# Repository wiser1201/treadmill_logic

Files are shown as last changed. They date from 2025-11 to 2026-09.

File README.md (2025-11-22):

# Description

This project replaces the entire logic/control section of a broken treadmill with a custom-designed **STM32** microcontroller-based control system. The power electronic part of the original board stayed intact, but the control MCU and interface electronics were redesigned to restore full functionality and improve usability. Firmware is written in **C** using **HAL** library and register access when needed.

IMG_treadmill

IMG_UI

# Hardware

### Components

- **Power PCB:** Reused robust power part of the original board;
- **Logic PCB:** Designed board that contains low-voltage supply + control logic;
- **Interface PCB:** Contains three buttons, and LCD 16x2;
- **MCU:** STM32 F103C6T6;

### Architecture

System uses phase angle control topology. The original power board contains an optocoupler that triggers a triac driving the 220 VAC power rail. After each zero-cross event, the triac naturally turns off; the moment at which it is fired determines what portion of each AC half-wave reaches the motor.

The logic PCB generates a zero-cross pulse using a transformer (13 VAC), rectifier, and an optocoupler. When the AC waveform rises above the LED threshold (~1.2 V), the optocoupler produces a clean pulse that marks each zero-crossing. STM32 receives this pulse, TIM1 in one pulse slave mode starts counting a delay automatically, and then, in the end of the delay, fires a short trigger pulse to the power-stage optocoupler, which in turn fires the main triac.

Motor speed is closed-loop controlled. The PID controller adjusts delay of TIM1 based on the current speed, calculated via RPM and a belt length. If current speed lower than target, PID decreases TIM1 delay, that gives more power to the triac. And vice versa.

# Software

### Architecture

Almost all software is divided into two layers: driver and application. 

- **Driver layer.** Low level code related to peripheral configuration, peripheral initialization.

- **Application layer.** Code, that's not related or not only related to peripherals. Software that built on top of the drivers, and corresponds to one specific use.

Some modules (such as simple Buttons or Buzzer) are too small to justify a strict driver/application separation. In these cases, the functionality is implemented in a single combined module to keep the code clean and avoid unnecessary fragmentation.

### Main loop

IMG_loop

The main loop coordinates the system's high-level tasks: motion control, fault monitoring, button handling**, **buzzer control, and LCD updates:

- **motion.** Executes the PID-based speed control described earlier, updating the phase-angle delay according to the current RPM feedback.
- **fault_check.** Monitors critical runtime conditions. It ensures that tim3, hall sensor and motion control work correctly.
- **buttons_handler.** Polls the user interface buttons (Start/Stop, Speed+, Speed–), debounces input, passes information to the system module.
- **buzzer.** Non-blocking audible feedback system.
- **LCD.** Periodically updates the 16×2 LCD with four metrics: Calories (C), Speed (S), Time (T), and Distance (D). The update routine is optimized to refresh only changed fields.

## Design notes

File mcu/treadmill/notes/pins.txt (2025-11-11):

PA8 - ZERO_CROSS;
PA9 - Trigger;
PB6-8 - Buttons;
PB5 - Buzzer;
PA7-1 - LCD;
PB4 - Hall;

pcb:
4 gnd, 4 +5V: (lcd, mcu, hall, +1 extra);
2 signals: buzzer, ZERO_CROSS

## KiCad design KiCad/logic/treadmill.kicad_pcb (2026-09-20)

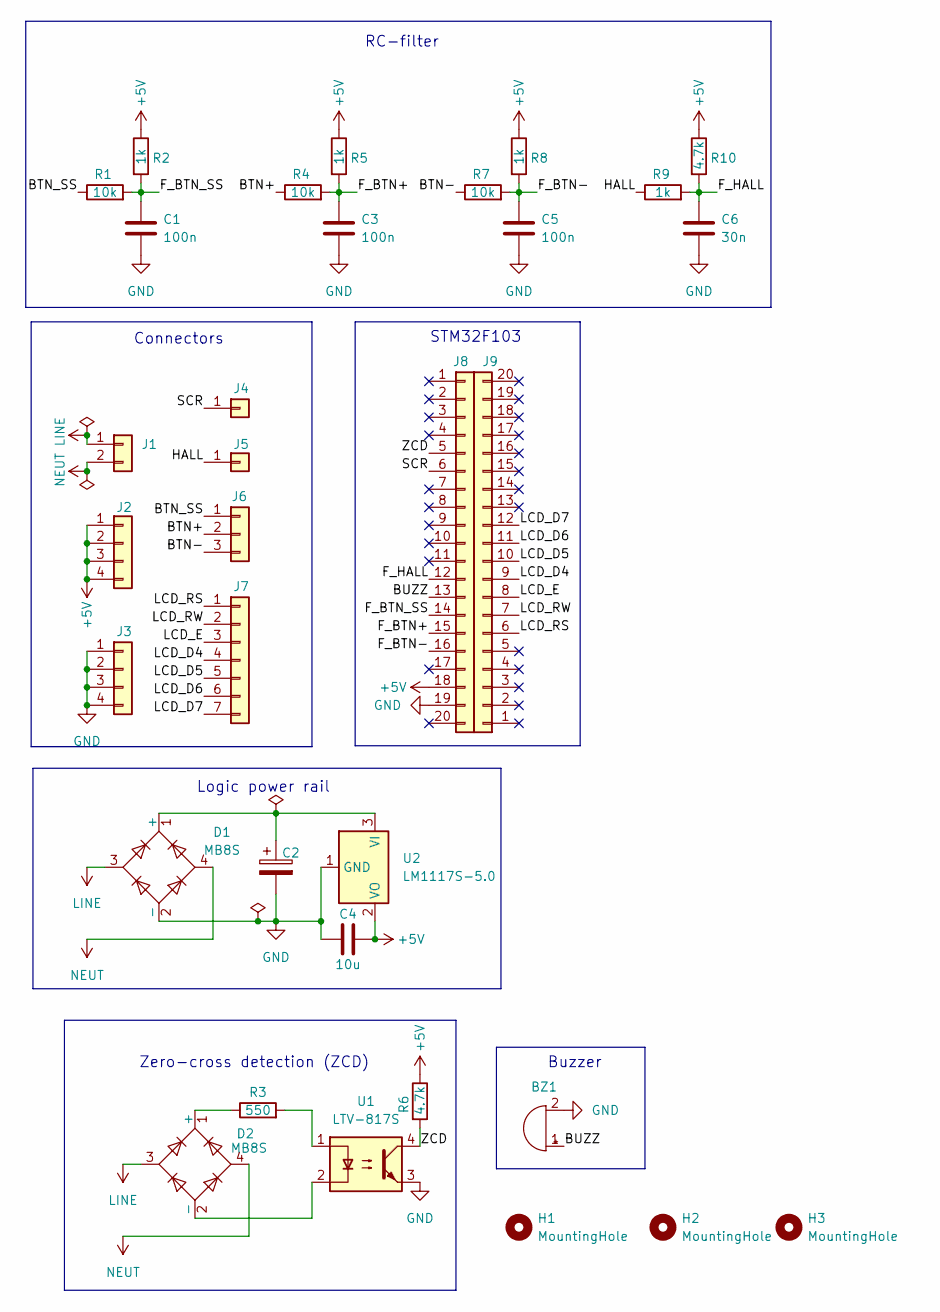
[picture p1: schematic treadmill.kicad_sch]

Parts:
BZ1: Buzzer; Buzzer_12x9.5RM7.6
C1, C3, C5: 100n; C_0805_2012Metric
C2: C_Polarized; CP_Radial_D13.0mm_P7.50mm
C4: 10u; C_0805_2012Metric
C6: 30n; C_0805_2012Metric
D1, D2: MB8S; OnSemi_751EP_SOIC-4_3.9x4.725mm_P2.54mm
H1, H2, H3: MountingHole; MountingHole_3.2mm_M3
J1: AC; TerminalBlock_Phoenix_MKDS-1,5-2_1x02_P5.00mm_Horizontal
J2: +5V; PinHeader_1x04_P2.54mm_Vertical
J3: GND; PinHeader_1x04_P2.54mm_Vertical
J4: SCR_01x01; PinHeader_1x01_P2.54mm_Vertical
J5: HALL_01x01; PinHeader_1x01_P2.54mm_Vertical
J6: BTN_01x03; PinSocket_1x03_P2.54mm_Vertical
J7: LCD_01x07; PinSocket_1x07_P2.54mm_Vertical
J8: MCU-1; PinSocket_1x20_P2.54mm_Vertical
J9: MCU-2; PinSocket_1x20_P2.54mm_Vertical
R1, R4, R7: 10k; R_0805_2012Metric
R2, R5, R8, R9: 1k; R_0805_2012Metric
R3: 550; R_2010_5025Metric
R6, R10: 4.7k; R_0805_2012Metric
U1: LTV-817S; SMDIP-4_W9.53mm
U2: LM1117S-5.0; SOT-223-3_TabPin2

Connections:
+5V: C4.2, J2.1, J2.2, J2.3, J2.4, J8.18, R2.1, R5.1, R6.1, R8.1, R10.1, U2.2 (VO)
/BTN+: J6.2, R4.1
/BTN-: J6.3, R7.1
/BTN_SS: J6.1, R1.1
/BUZZ: BZ1.1 (+), J8.13
/F_BTN+: C3.1, J8.15, R4.2, R5.2
/F_BTN-: C5.1, J8.16, R7.2, R8.2
/F_BTN_SS: C1.1, J8.14, R1.2, R2.2
/F_HALL: C6.1, J8.12, R9.2, R10.2
/HALL: J5.1, R9.1
/LCD_D4: J7.4, J9.9
/LCD_D5: J7.5, J9.10
/LCD_D6: J7.6, J9.11
/LCD_D7: J7.7, J9.12
/LCD_E: J7.3, J9.8
/LCD_RS: J7.1, J9.6
/LCD_RW: J7.2, J9.7
/SCR: J4.1, J8.6
/ZCD: J8.5, R6.2, U1.4
GND: BZ1.2 (-), C1.2, C2.2, C3.2, C4.1, C5.2, C6.2, D1.2 (-), J3.1, J3.2, J3.3, J3.4, J8.19, U1.3, U2.1 (GND)
LINE: D1.3, D2.3, J1.1
NEUT: D1.4, D2.4, J1.2
unnamed: C2.1, D1.1 (+), U2.3 (VI)
unnamed: D2.1 (+), R3.1
unnamed: D2.2 (-), U1.2
unnamed: R3.2, U1.1

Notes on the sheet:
Buzzer
Zero-cross detection (ZCD)
Logic power rail
Connectors
RC-filter
STM32F103

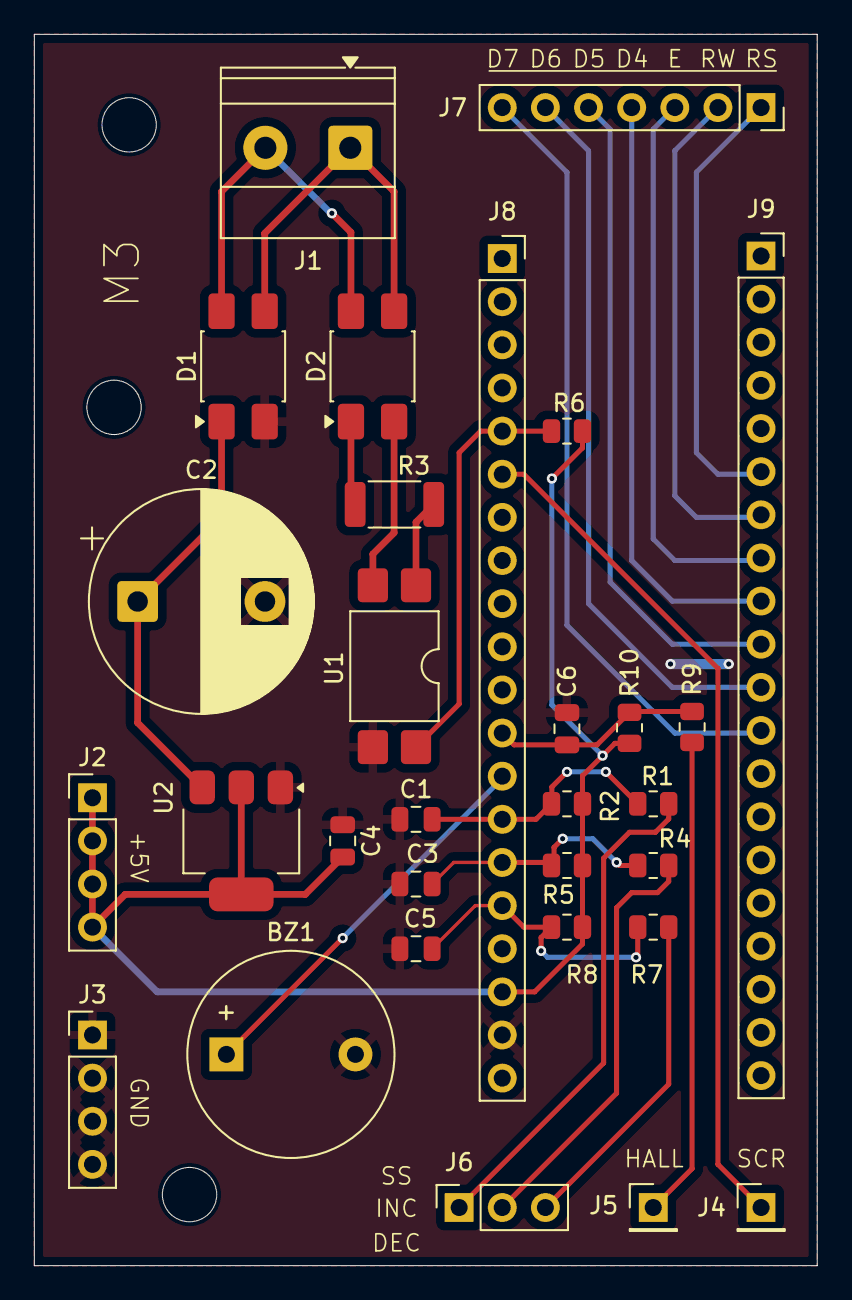
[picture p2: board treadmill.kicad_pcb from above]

Board: 2 copper layers, 46.1 x 72.5 mm, 33 parts (0 on the bottom side), 26 nets.

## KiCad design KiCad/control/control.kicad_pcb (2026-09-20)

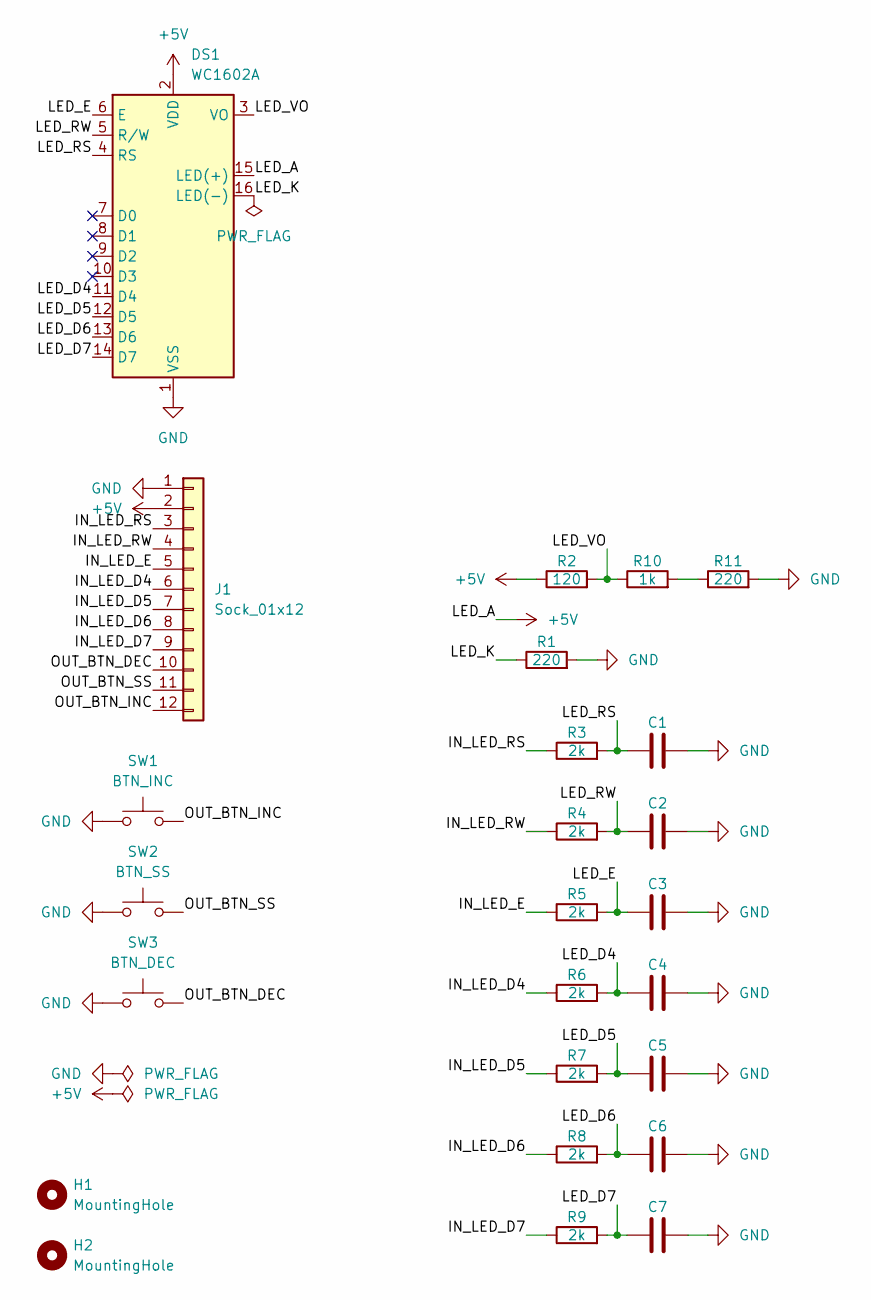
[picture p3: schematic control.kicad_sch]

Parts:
C1, C2, C3, C4, C5, C6, C7: 1n; C_0805_2012Metric
DS1: WC1602A
H1, H2: MountingHole; MountingHole_2.7mm
J1: Sock_01x12; PinSocket_1x12_P2.54mm_Vertical
R1, R11: 220; R_1210_3225Metric
R2: 120; R_1210_3225Metric
R3, R4, R5, R6, R7, R8, R9: 2k; R_0805_2012Metric
R10: 1k; R_1210_3225Metric
SW1: BTN_INC; SW_PUSH-12mm
SW2: BTN_SS; SW_PUSH-12mm
SW3: BTN_DEC; SW_PUSH-12mm

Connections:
+5V: DS1.2 (VDD), DS1.15 (LED(+)), J1.2, R2.1
/IN_LED_D4: J1.6, R6.1
/IN_LED_D5: J1.7, R7.1
/IN_LED_D6: J1.8, R8.1
/IN_LED_D7: J1.9, R9.1
/IN_LED_E: J1.5, R5.1
/IN_LED_RS: J1.3, R3.1
/IN_LED_RW: J1.4, R4.1
/LED_D4: C4.2, DS1.11 (D4), R6.2
/LED_D5: C5.2, DS1.12 (D5), R7.2
/LED_D6: C6.2, DS1.13 (D6), R8.2
/LED_D7: C7.2, DS1.14 (D7), R9.2
/LED_E: C3.2, DS1.6 (E), R5.2
/LED_K: DS1.16 (LED(-)), R1.1
/LED_RS: C1.2, DS1.4 (RS), R3.2
/LED_RW: C2.2, DS1.5 (R/W), R4.2
/LED_VO: DS1.3 (VO), R2.2, R10.1
/OUT_BTN_DEC: J1.10, SW3.2
/OUT_BTN_INC: J1.12, SW1.2
/OUT_BTN_SS: J1.11, SW2.2
GND: C1.1, C2.1, C3.1, C4.1, C5.1, C6.1, C7.1, DS1.1 (VSS), J1.1, R1.2, R11.2, SW1.1, SW2.1, SW3.1
unnamed: R10.2, R11.1

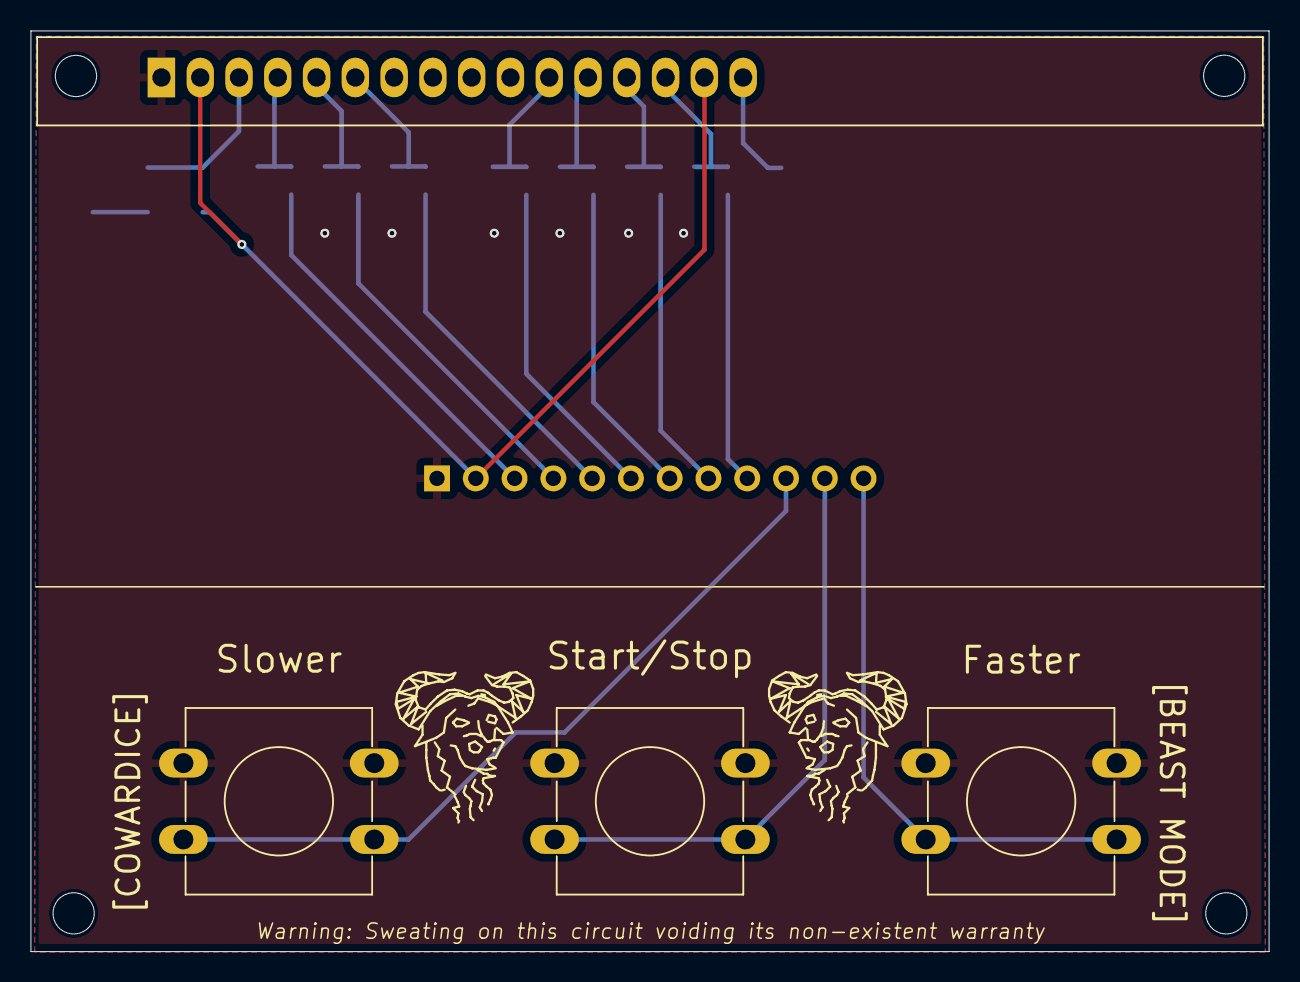
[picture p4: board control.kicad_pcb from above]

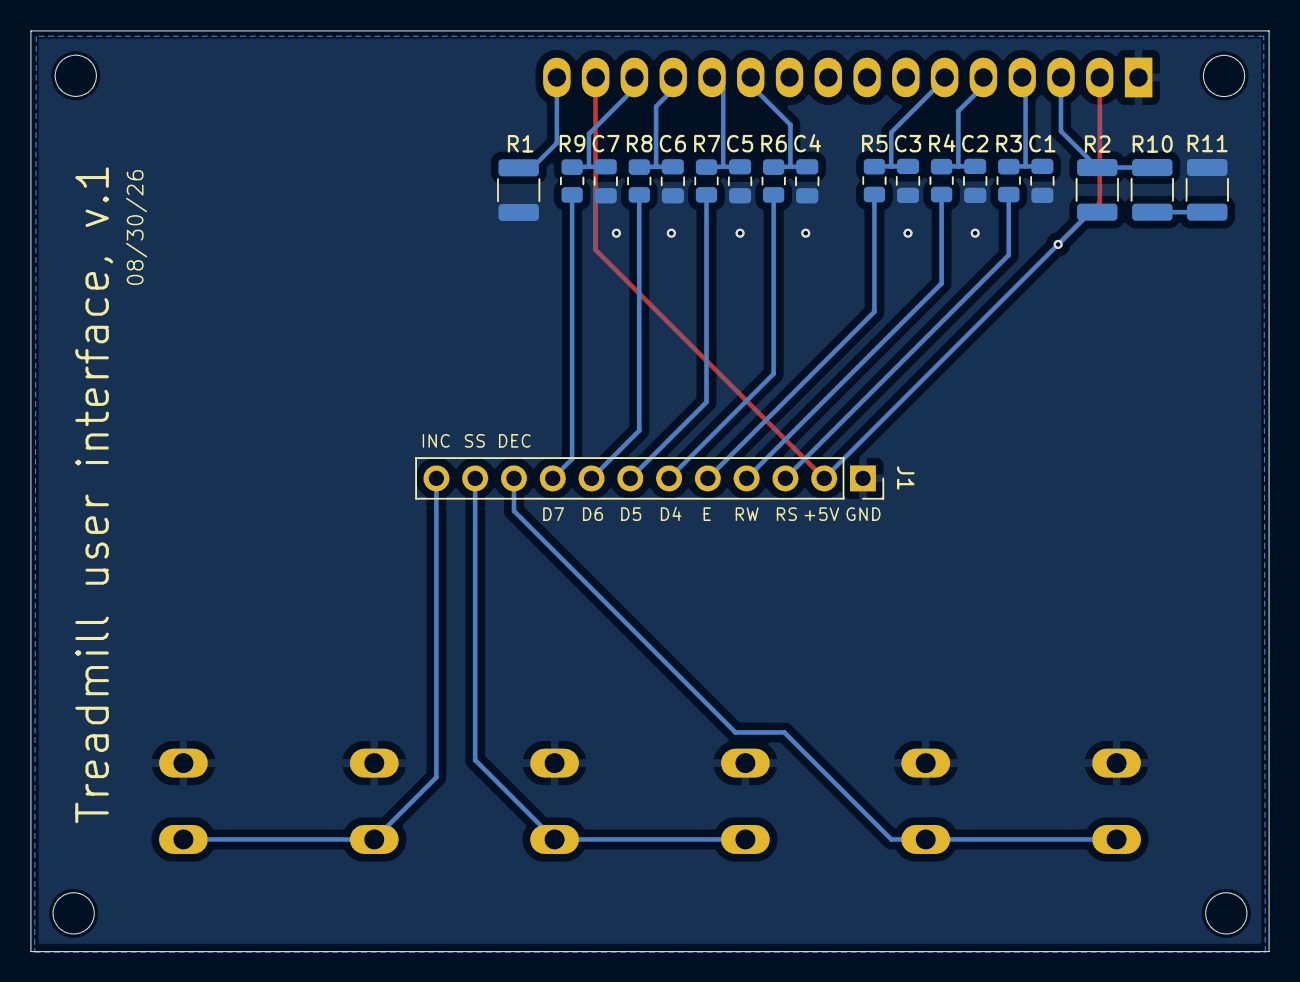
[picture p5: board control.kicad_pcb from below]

Board: 2 copper layers, 81.1 x 60.3 mm, 25 parts (19 on the bottom side), 22 nets.

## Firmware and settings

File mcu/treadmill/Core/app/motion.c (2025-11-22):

#include "motion.h"
#include "tim1.h"
#include "hall.h"
#include "time.h"
#include <math.h>
#include <stdint.h>
#include <stdlib.h>

#define SPEED_MAX 12
#define SPEED_MIN 4
#define SOFT_START_DELAY 1500
#define SINE_PERIOD 20000
#define TRIG_LATENCY 300
#define DEAD_TIME 500
#define MIN_SPEED_SHIFT 1900
#define PERIOD_MAX ((SINE_PERIOD / 2) - TRIG_LATENCY - DEAD_TIME - MIN_SPEED_SHIFT)
#define PERIOD_MIN ((SINE_PERIOD / 2) * 0.4)

typedef struct
{
    const float Kp;
    const float Ki;
    const float Kd;
    float i_pr;
    float error_pr;
    float error;
    const int min;
    const int max;
    const float hyst;
} PID_Data;

static int targ_speed = SPEED_MIN;
static float curr_speed = 0;
static PID_Data pid_data = 
{
    .Kp = 100.f,
    .Ki = 4000.f,
    .Kd = 70.f,
    .min = 0,
    .max = PERIOD_MAX - PERIOD_MIN,
    .hyst = 0.1f
};

static int clamp(int val, int min, int max);
static int pid_calc(PID_Data* data);

void motion_tick(void)
{
    const float roller_diam = 0.05023;
    const float time_const = 0.06f;
    const uint32_t rpm = hall_sampled() ? hall_getRPM() : hall_getPrevRPM();
    curr_speed = M_PI * roller_diam * rpm * time_const;
    pid_data.error = targ_speed - curr_speed;
    if (abs(pid_data.error) > pid_data.hyst)
    {
        int period = PERIOD_MAX + (-pid_calc(&pid_data));
        if (tim1_getPeriod() != period)
        {
            tim1_setPeriod(period);
        }
    }
}

void motion_reset(void)
{
    curr_speed = 0;
    pid_data.error = 0;
    pid_data.error_pr = 0;
    pid_data.i_pr = 0;
}

void motion_softStart(void)
{
    tim1_setPeriod(PERIOD_MAX);
    const uint32_t timeout = time_ms() + SOFT_START_DELAY;
    while (time_ms() < timeout) {}
}

int pid_calc(PID_Data* data)
{
    const int tick_us = 10;
    const float sample_period_sec = tick_us / 1000000.f;
    float p_part = data->Kp * data->error;
    float i_part = data->i_pr + data->Ki * sample_period_sec * data->error;
    float d_part = data->Kd * ((data->error - data->error_pr));
    int actuating_signal = p_part + i_part + d_part;
    int clamped = clamp(actuating_signal, data->min, data->max);

    if (actuating_signal < data->min)
    {
        if (data->error > 0)
        {
            data->i_pr = i_part;
        }
    }
    else if (actuating_signal > data->max)
    {
        if (data->error < 0)
        {
            data->i_pr = i_part;
        }
    }
    else
    {
        data->i_pr = i_part;
    }
    data->error_pr = data->error;

    return clamped;
}

int clamp(int val, int min, int max)
{
    return val < min ? min : val > max ? max : val;
}

int motion_getSpeed(void)
{
    return targ_speed;
}

int motion_getCurrSpeed(void)
{
    return curr_speed;
}

void motion_incrSpeed(void)
{
    if ((targ_speed + 1) <= SPEED_MAX)
    {
        ++targ_speed;
    }
}

void motion_decrSpeed(void)
{
    if ((targ_speed - 1) >= SPEED_MIN)
    {
        --targ_speed;
    }
}

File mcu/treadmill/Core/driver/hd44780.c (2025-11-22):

#include "hd44780.h"

/* Instructions */
#define I_CLS (1 << 0)
#define I_RET_HOME (1 << 1)
#define I_MODE_SET (1 << 2)
#define I_ON_OFF (1 << 3)
#define I_SHIFT (1 << 4)
#define I_FUNC_SET (1 << 5)
#define I_SET_CG_ADDR (1 << 6)
#define I_SET_DD_ADDR (1 << 7)

/* Flags */
#define F_ID 1  // I_MODE_SET; INCR = 1, DECR = 0;
#define F_S 0   // I_MODE_SET; SHIFT DISAPLY = 1, NOP = 0;
#define F_D 2   // I_ON_OFF; DISPLAY ON = 1, DISPLAY OFF = 0;
#define F_C 1   // I_ON_OFF; CURSOR ON = 1, CURSOR OFF = 0;
#define F_B 0   // I_ON_OFF; BLINK ON = 1, BLINK OFF = 0;
#define F_SC 3  // I_SHIFT; DISPLAY MOVE = 1, CURSOR MOVE = 0;
#define F_RL 2  // I_SHIFT; RIGHT = 1, LEFT = 0;
#define F_DL 4  // I_FUNC_SET; DATA LENGTH 8 = 1, DL 4 = 0;
#define F_N 3   // I_FUNC_SET; LINES 2 = 1, LINES 1 = 0;
#define F_F 2   // I_FUNC_SET; FONT 5x10 = 1, FONT 5x8 = 0;
#define F_BF 7  // BUSY FLAG, read status reg

#define FLAG_IS_SET(reg, flag) ((reg) & (1 << (flag)))
#define SET_FLAG(reg, flag)    ((reg) |= (1 << (flag)))
#define CLEAR_FLAG(reg, flag)  ((reg) &= ~(1 << (flag)))
#define TOGGLE_FLAG(reg, flag) ((reg) ^= (1 << (flag)))

#define HIGH 1
#define LOW 0

/* Extern board-specific functions must be implemented in user code */
extern void ex_delay_us(const uint32_t us);
extern void ex_gpio_config(const HD44780_Pin_e pin, const DataDirection_e dir);
extern void ex_gpio_write(const HD44780_Pin_e pin, const bool level);
extern bool ex_gpio_read(const HD44780_Pin_e pin);


/* Communication protocol driver section */
#define NUM_OF_DL 8 
#define NUM_OF_USED_DL 4 // num of used data lines
#define PULSE_US 100
#define GAP_US (PULSE_US / 2)
#define PERIOD_US ((PULSE_US * 2 + GAP_US) * 2) // two pulses (4 + 4 bits data) + gap in-between

static DataDirection_e dataDir = DD_INPUT;

static void parallel_tx(const bool rs, const uint8_t data); // transmit
static uint8_t parallel_rx(const bool rs); // receive
static void parallel_cdd(void); // change data direction
static bool wait_for_unbusy_flag(void);

void parallel_tx(const bool rs, const uint8_t data)
{
    if (wait_for_unbusy_flag() == false)
    {
        return;
    }

    if (dataDir != DD_OUTPUT)
    {
        parallel_cdd();
    }

    ex_gpio_write(HDP_ENABLE, LOW);
    ex_gpio_write(HDP_RS, rs);
    ex_gpio_write(HDP_RW, LOW);

    const int msb = 7;
    const int numOfStages = NUM_OF_DL / NUM_OF_USED_DL;
    const int lsp = NUM_OF_DL / numOfStages;
    for (int stage = 0, bit_i = msb; stage < numOfStages; ++stage)
    {
        for (int pin_i = msb; pin_i >= lsp && bit_i >= 0; --pin_i, --bit_i)
        {
            ex_gpio_write((HD44780_Pin_e)pin_i, FLAG_IS_SET(data, bit_i));
        }
        ex_gpio_write(HDP_ENABLE, HIGH);
        ex_delay_us(PULSE_US);
        ex_gpio_write(HDP_ENABLE, LOW);
        ex_delay_us(GAP_US);
    }
}

uint8_t parallel_rx(const bool rs)
{
    if (rs)
    {
        if (wait_for_unbusy_flag() == false)
        {
            return 0xFF;
        }
    }

    if (dataDir != DD_INPUT)
    {
        parallel_cdd();
    }

    ex_gpio_write(HDP_ENABLE, LOW);
    ex_gpio_write(HDP_RS, rs);
    ex_gpio_write(HDP_RW, HIGH);

    uint8_t ret = 0;
    const int msb = 7;
    const int numOfStages = NUM_OF_DL / NUM_OF_USED_DL;
    const int lsp = NUM_OF_DL / numOfStages; // last pin
    for (int stage = 0, bit_i = msb; stage < numOfStages; ++stage)
    {
        ex_gpio_write(HDP_ENABLE, HIGH);
        ex_delay_us(PULSE_US);
        for (int pin_i = msb; pin_i >= lsp && bit_i >= 0; --pin_i, --bit_i)
        {
            const uint8_t signal = ex_gpio_read((HD44780_Pin_e)pin_i);
            ret |= (signal << bit_i);
        }
        ex_gpio_write(HDP_ENABLE, LOW);
        ex_delay_us(GAP_US);
    }
    return ret;
}

void parallel_cdd(void)
{
    DataDirection_e target_dir = !dataDir;

    for (int pin = 7; pin >= NUM_OF_USED_DL; --pin)
    {
        ex_gpio_config((HD44780_Pin_e)pin, target_dir);
    }
    dataDir = target_dir;
}

bool wait_for_unbusy_flag(void)
{
    ex_delay_us(2000);
    return true;
}
/* ~Communication protocol driver section end */

/* LCD driver section */
#define DISPLAY_X_LENGTH 16
#define DISPLAY_Y_LENGTH 2
#define DISPLAY_Y_ADDR_SHIFT 0x40

void hd44780_init(void)
{
    ex_gpio_config(HDP_RS, DD_OUTPUT);
    ex_gpio_config(HDP_RW, DD_OUTPUT);
    ex_gpio_config(HDP_ENABLE, DD_OUTPUT);
    dataDir = DD_OUTPUT; // it's input by default, it's just for swap
    parallel_cdd();     // now D4-D7 are initialized as inputs

    /* for some reason my module requires exactly 2 cycles 
    of initialization. It doesn't work with just 1 */
    for (int i = 0; i < 2; ++i)
    {
        uint8_t func_set = I_FUNC_SET;
        SET_FLAG(func_set, F_N);
        parallel_tx(LOW, func_set);

        uint8_t on_off = I_ON_OFF;
        SET_FLAG(on_off, F_D);
        // SET_FLAG(on_off, F_C);
        // SET_FLAG(on_off, F_B);
        parallel_tx(LOW, on_off);

        uint8_t mode_set = I_MODE_SET;
        SET_FLAG(mode_set, F_ID);
        parallel_tx(LOW, mode_set);

        uint8_t clear_display = I_CLS;
        parallel_tx(LOW, clear_display);

        uint8_t set_dd_addr = I_SET_DD_ADDR;
        parallel_tx(LOW, set_dd_addr);
    }
}

void hd44780_print(const uint8_t x, const uint8_t y, const char ch)
{
    if (x >= DISPLAY_X_LENGTH || y >= DISPLAY_Y_LENGTH)
    {
        return;
    }

    uint8_t addr = x + y * DISPLAY_Y_ADDR_SHIFT;
    parallel_tx(LOW, addr | I_SET_DD_ADDR);
    parallel_tx(HIGH, ch);
}

void hd44870_printLine(const uint8_t x, const uint8_t y, const char *str)
{
    if (x >= DISPLAY_X_LENGTH || y >= DISPLAY_Y_LENGTH)
    {
        return;
    }

    uint8_t addr = x + y * DISPLAY_Y_ADDR_SHIFT;
    parallel_tx(LOW, addr | I_SET_DD_ADDR);
    uint8_t mode_set = I_MODE_SET;
    parallel_tx(LOW, mode_set);

    for (const char* ptr = str; *ptr != '\0'; ++ptr)
    {
        parallel_tx(HIGH, *ptr);
    }
}
/* LCD driver section end */

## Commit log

2025-11-11 Init commit MCU code contains nothing, scheme and pcb has been already done.
    [treadmill_v2.kicad_pcb, treadmill_v2.kicad_sch]
2025-11-11 Addition: tim1 tim1 logic consists of basic init/start/stop/reset. One pulse mode. Tested. By default OC disabled (CCR = period + 1 while mode is PWM2, so disabled).
    [tim1.c]
2025-11-11 Feat: tim1: get/set period app needs this feature. setPeriod automatically sets CCR channel as period - TIMER1_PULSE_US.
2025-11-16 Release Stable tested version. Speed regulation a little bit floating when error becomes small. But in general, good job.
    [buttons.c, fault.c, hall.c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]
2025-11-30 fix: timer formula Pervious formula worked just fine. But from a sanity perspective, it was a nonsense.
